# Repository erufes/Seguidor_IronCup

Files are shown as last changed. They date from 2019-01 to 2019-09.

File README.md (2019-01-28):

# Seguidor_IronCup
O objetivo deste projeto é construir e aprimorar um seguidor de linha capaz de ganhar a competição da IronCup 2019. Para isso, o projeto consta de estudo, prototipagem, desing e aprimoramento.  https://www.robocore.net/eventos/ironcup-2019  Edital da competição: https://www.robocore.net/upload/attachments/robocore__regras_seguidor_de_linha_108.pdf

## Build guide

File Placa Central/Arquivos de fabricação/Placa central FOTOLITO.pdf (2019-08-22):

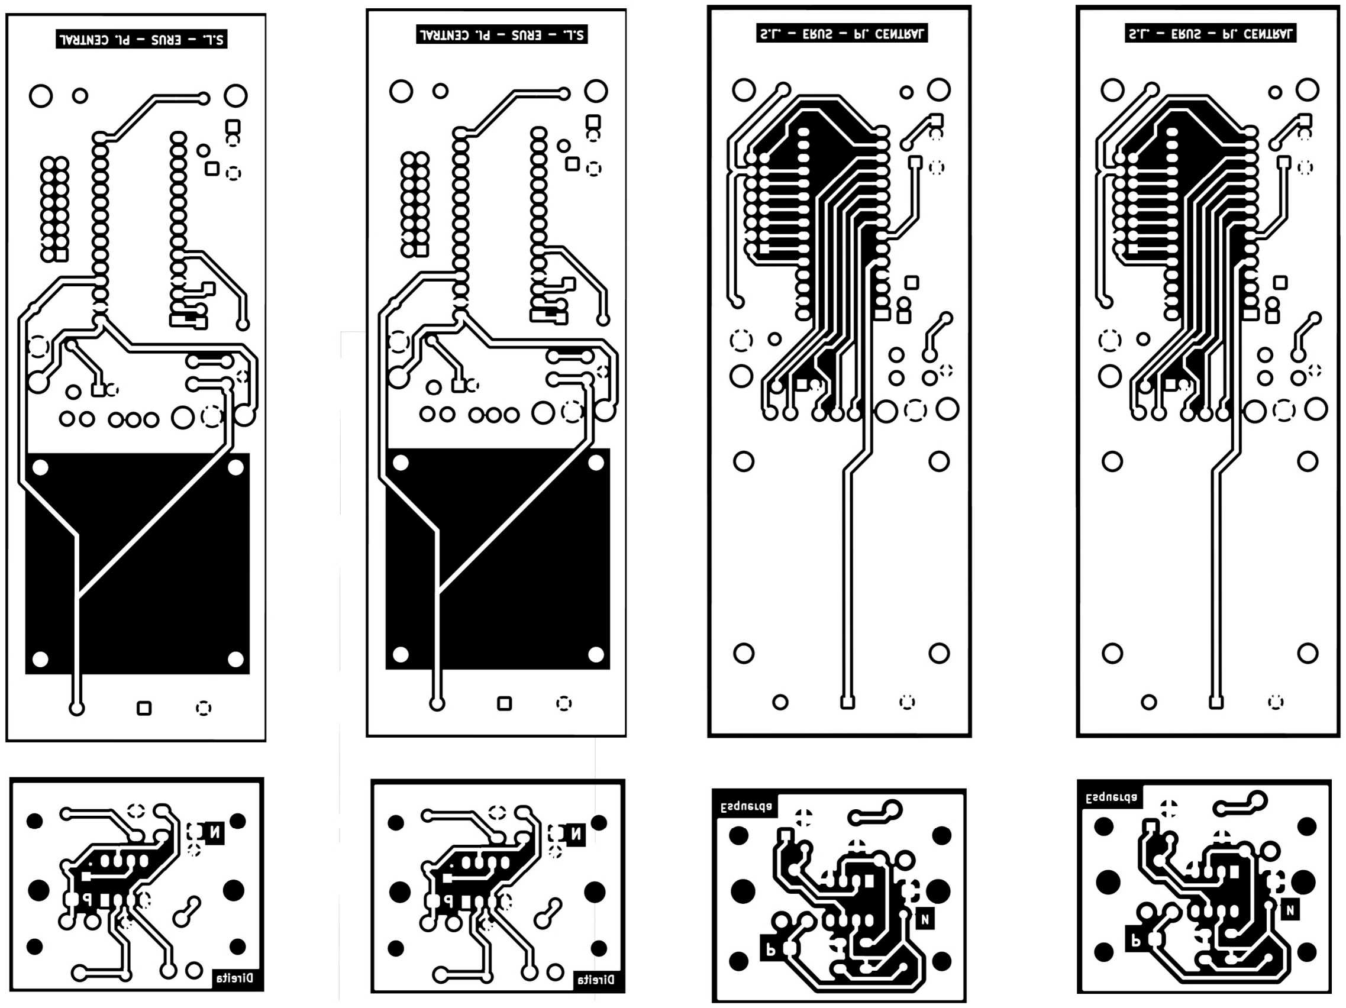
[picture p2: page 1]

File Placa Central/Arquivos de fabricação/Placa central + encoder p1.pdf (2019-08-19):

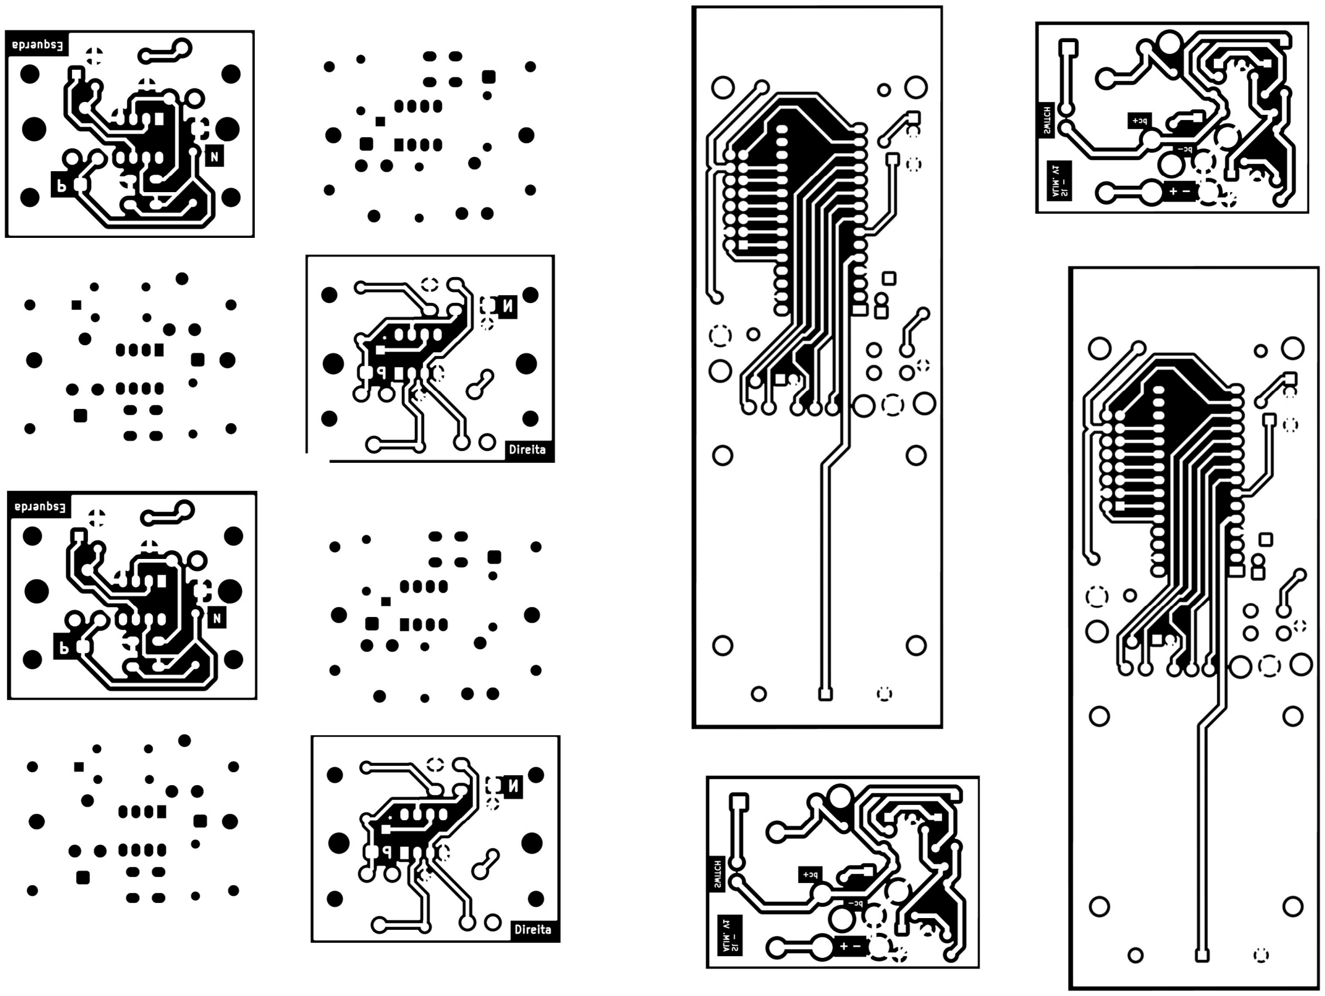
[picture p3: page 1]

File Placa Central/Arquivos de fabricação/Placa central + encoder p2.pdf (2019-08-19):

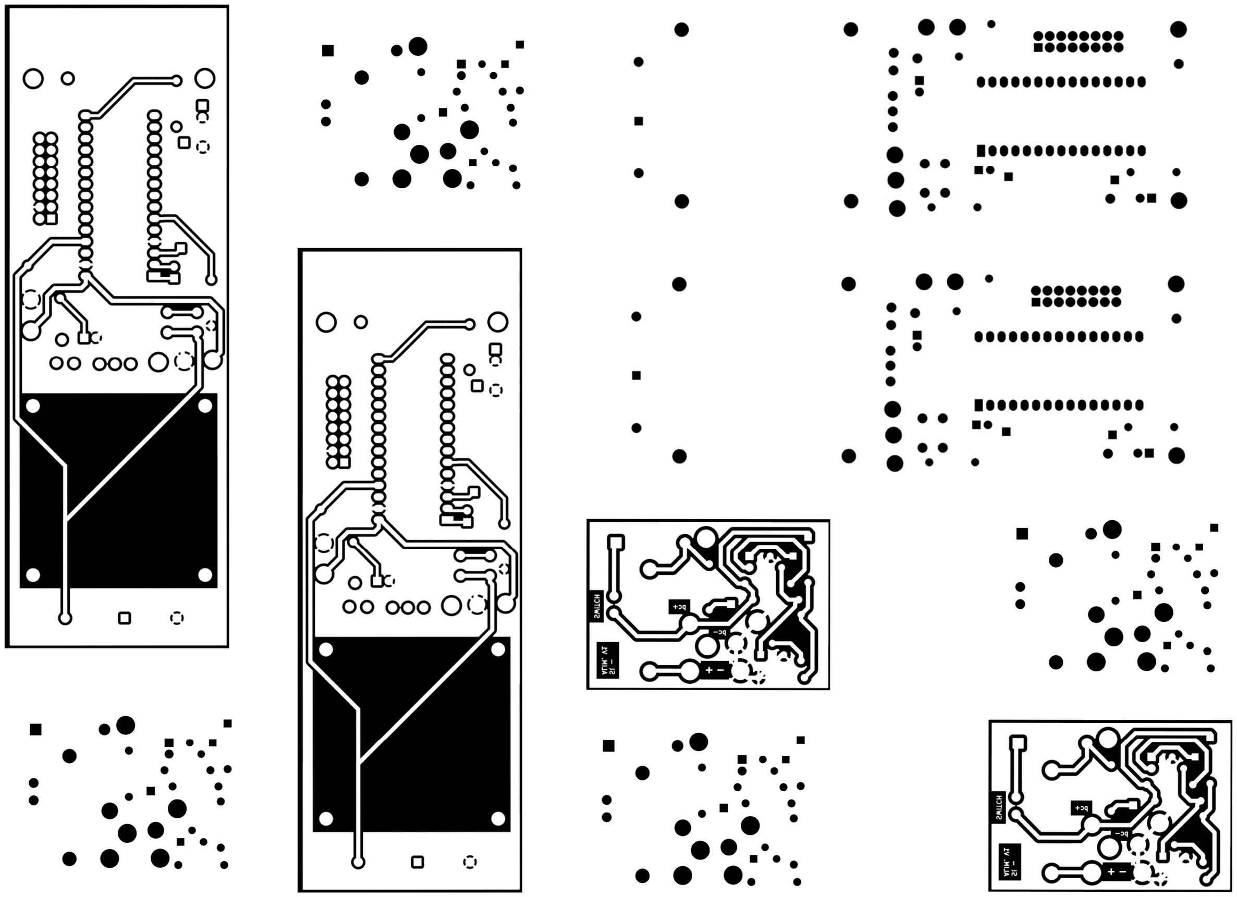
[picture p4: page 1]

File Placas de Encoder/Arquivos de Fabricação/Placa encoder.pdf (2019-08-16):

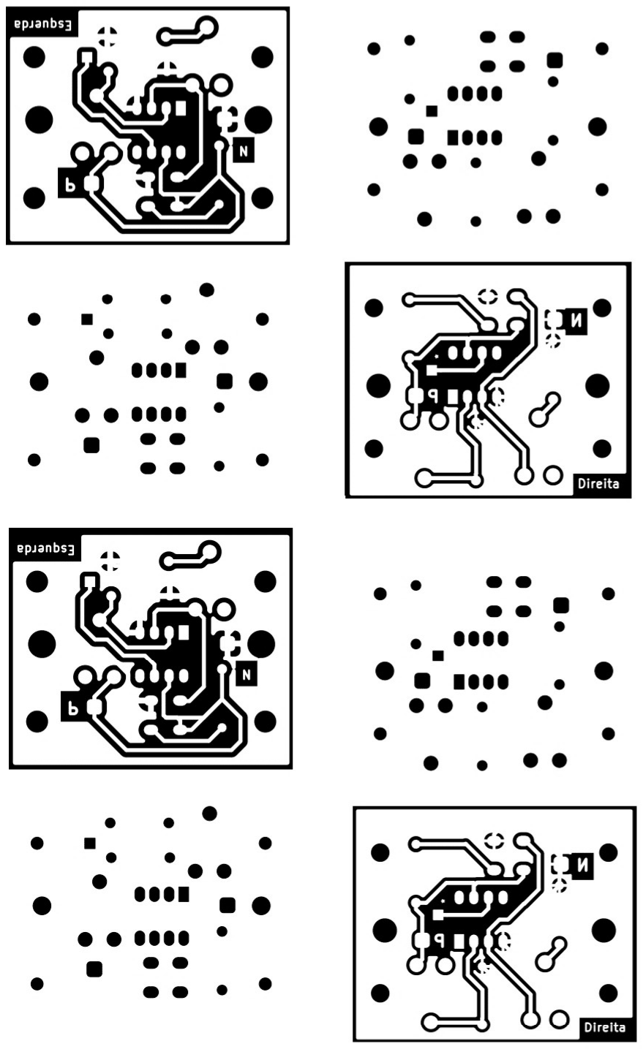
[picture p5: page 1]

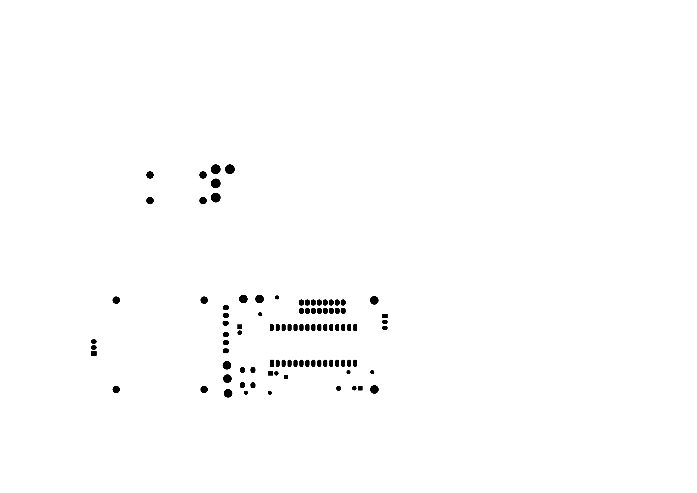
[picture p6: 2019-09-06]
Placa Central/Arquivos de fabricação/v1.1/Placa_central_v01-B_Mask_p001.png

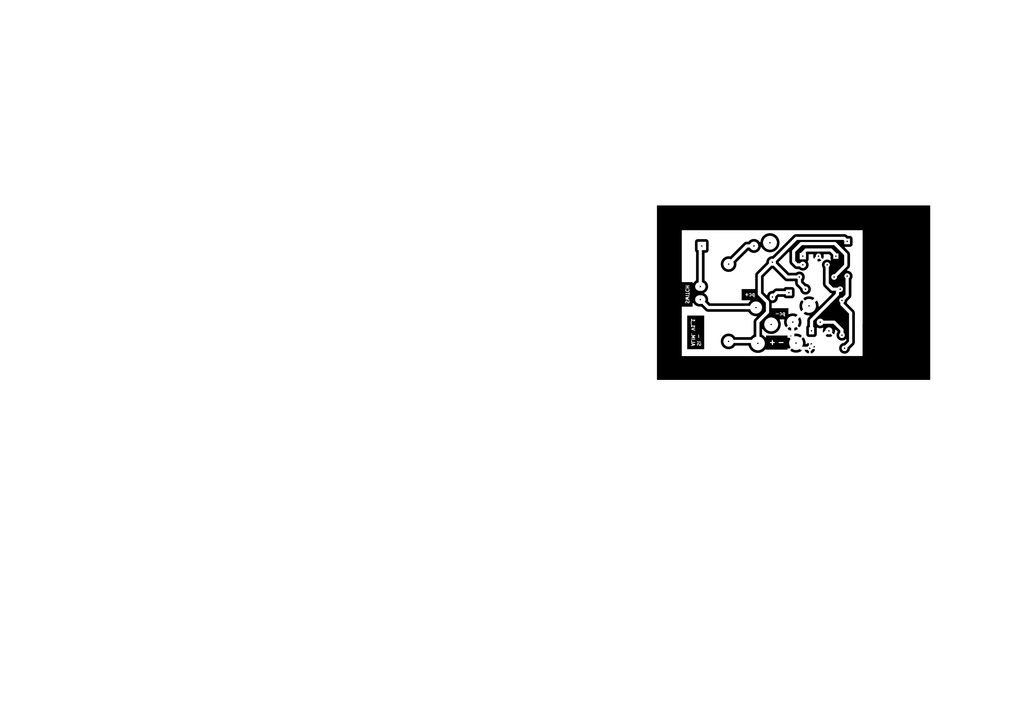
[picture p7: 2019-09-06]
Placa Central/Arquivos de fabricação/v1.1/Alimentacao e protecao-B_Cu_p001.png

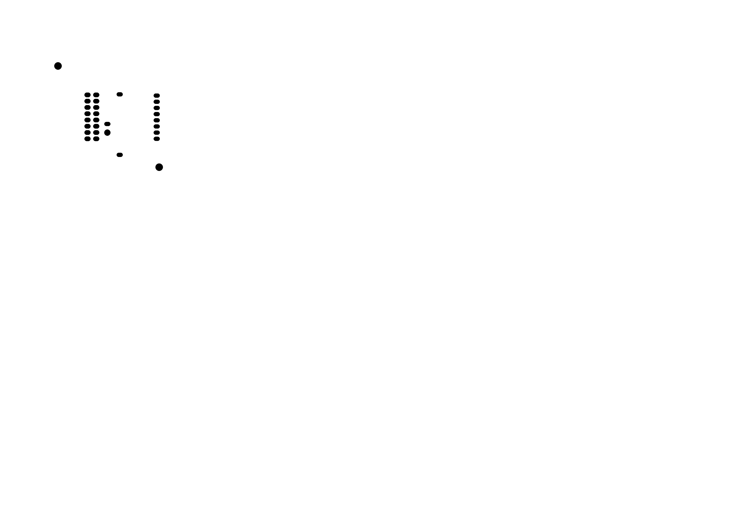
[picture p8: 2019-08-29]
Placa sensores/Placa_sensores v1_2/Placa de conexão/Arquivos de fabricação/Placa_sensores_v1_2 - Conector QTR-B_Mask_p001.png

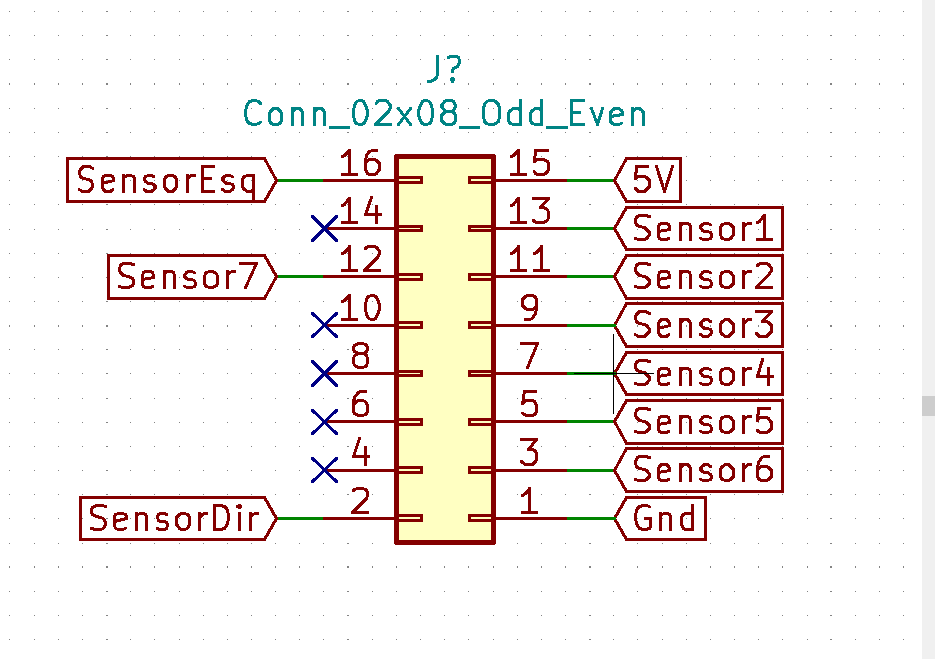
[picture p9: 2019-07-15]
Placa sensores/Placa_sensores v1_2/Placa de conexão/PrintConnectorPlacaSensores.png

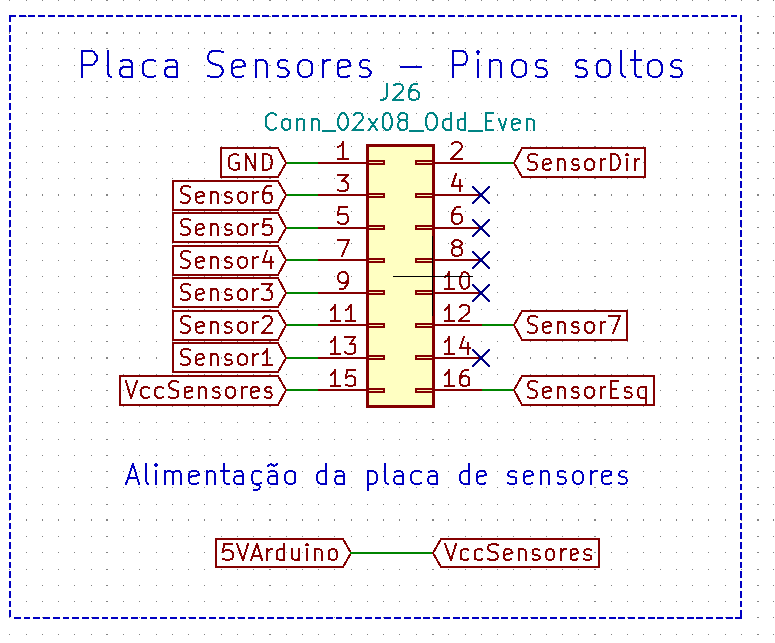
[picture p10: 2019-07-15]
Placa Central/PrintConnector.png

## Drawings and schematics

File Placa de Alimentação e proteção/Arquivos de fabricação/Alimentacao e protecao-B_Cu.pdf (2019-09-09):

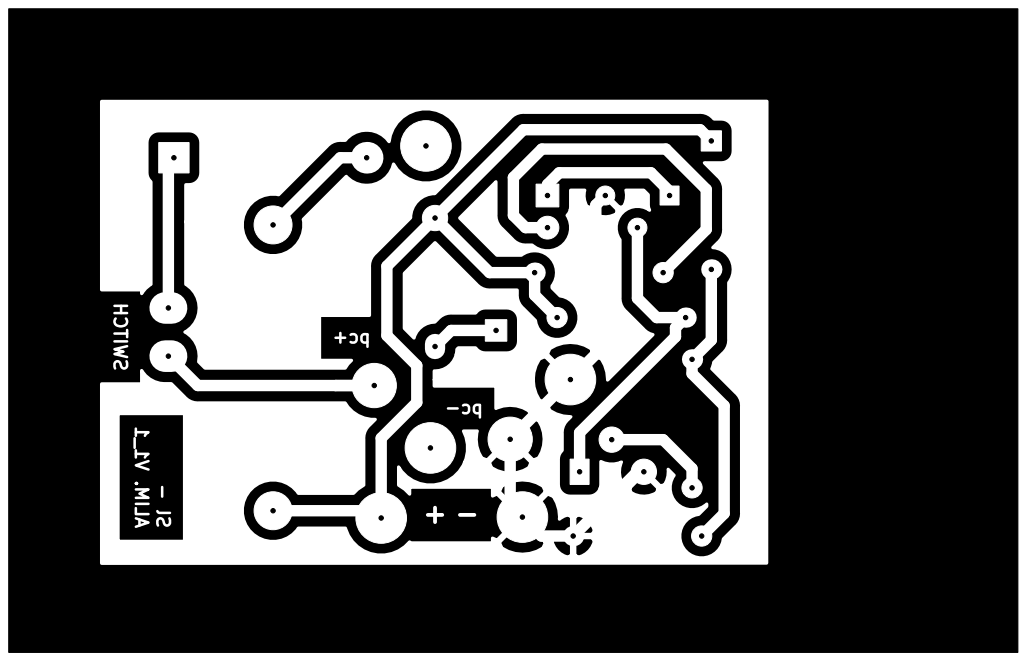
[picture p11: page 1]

ALIM. V1_1 Sl - + - pc+ pc- SWITCH

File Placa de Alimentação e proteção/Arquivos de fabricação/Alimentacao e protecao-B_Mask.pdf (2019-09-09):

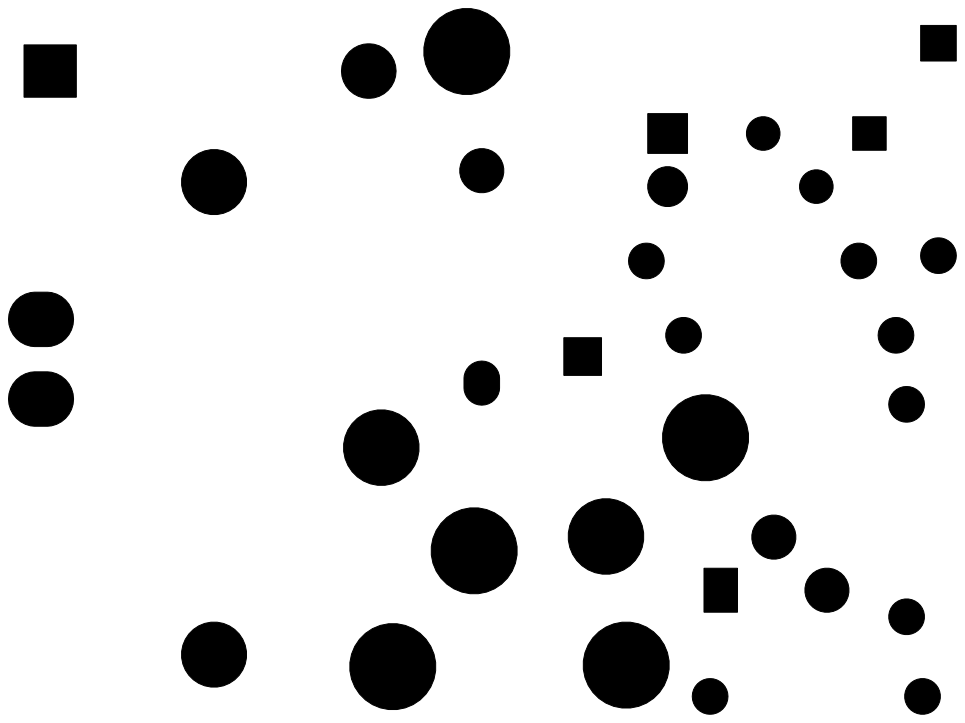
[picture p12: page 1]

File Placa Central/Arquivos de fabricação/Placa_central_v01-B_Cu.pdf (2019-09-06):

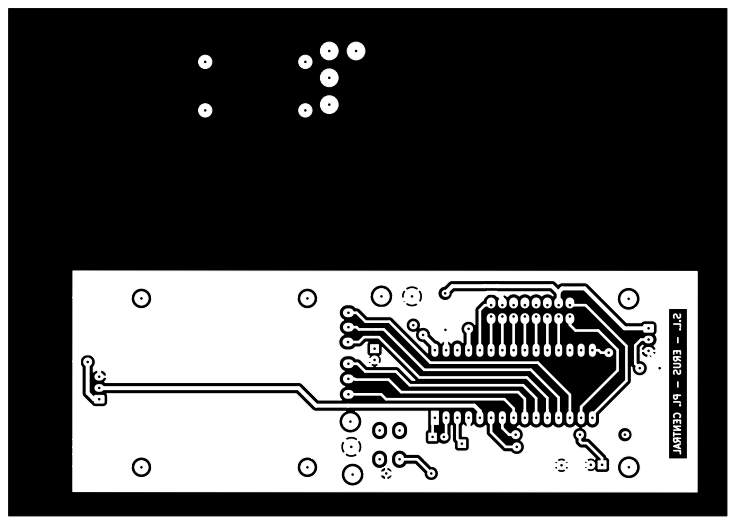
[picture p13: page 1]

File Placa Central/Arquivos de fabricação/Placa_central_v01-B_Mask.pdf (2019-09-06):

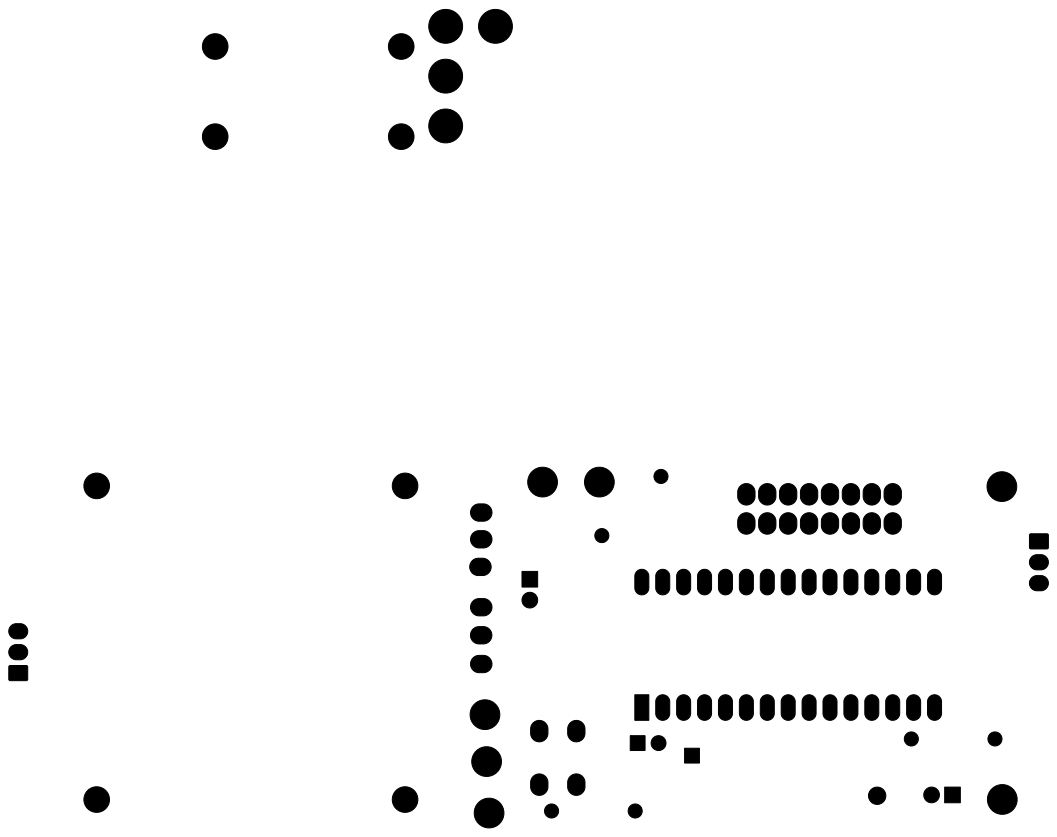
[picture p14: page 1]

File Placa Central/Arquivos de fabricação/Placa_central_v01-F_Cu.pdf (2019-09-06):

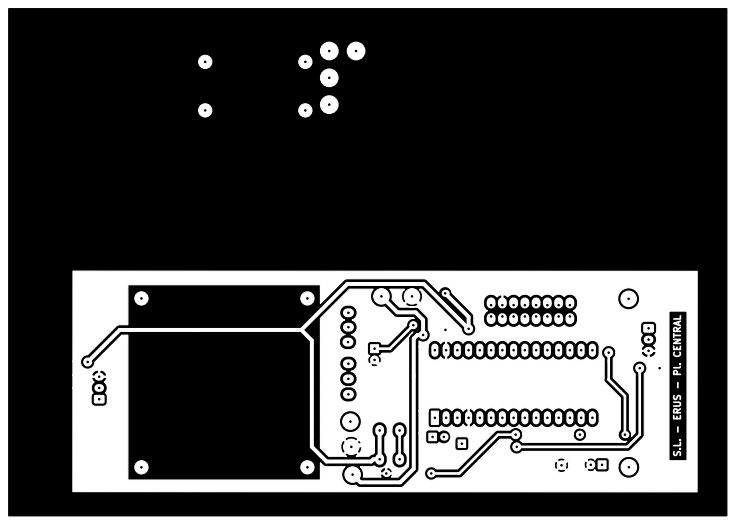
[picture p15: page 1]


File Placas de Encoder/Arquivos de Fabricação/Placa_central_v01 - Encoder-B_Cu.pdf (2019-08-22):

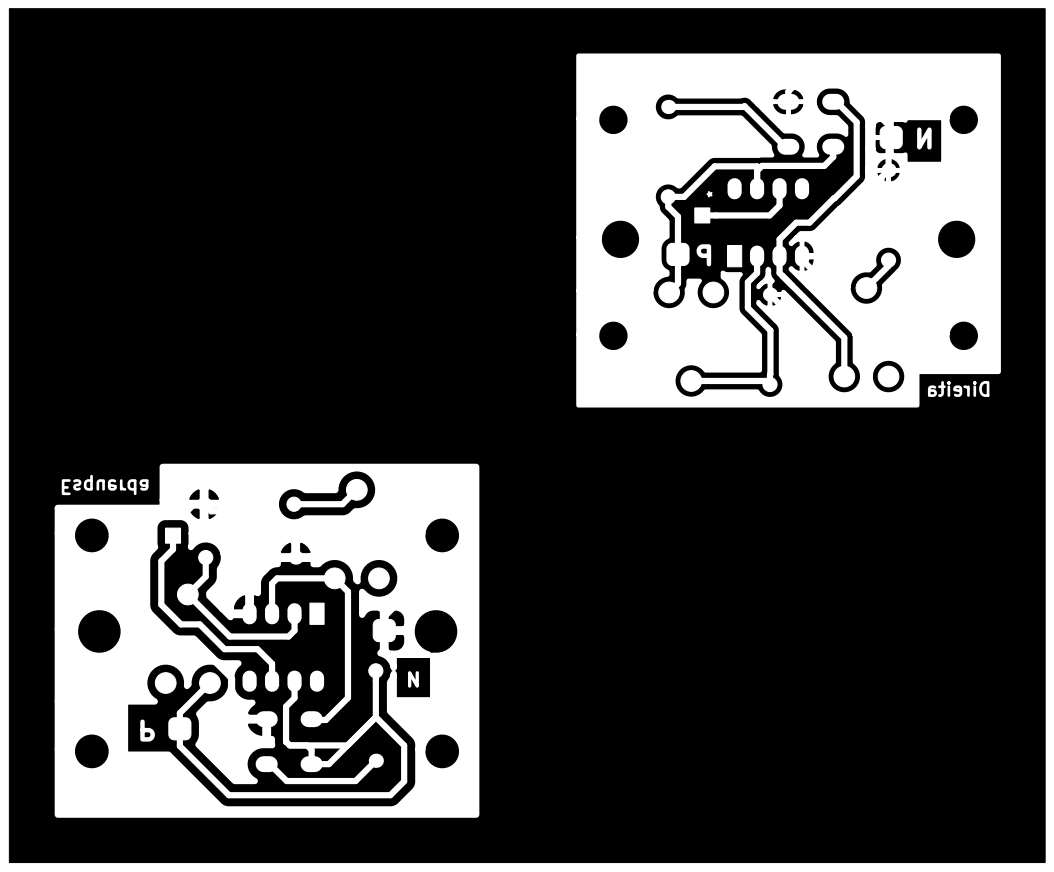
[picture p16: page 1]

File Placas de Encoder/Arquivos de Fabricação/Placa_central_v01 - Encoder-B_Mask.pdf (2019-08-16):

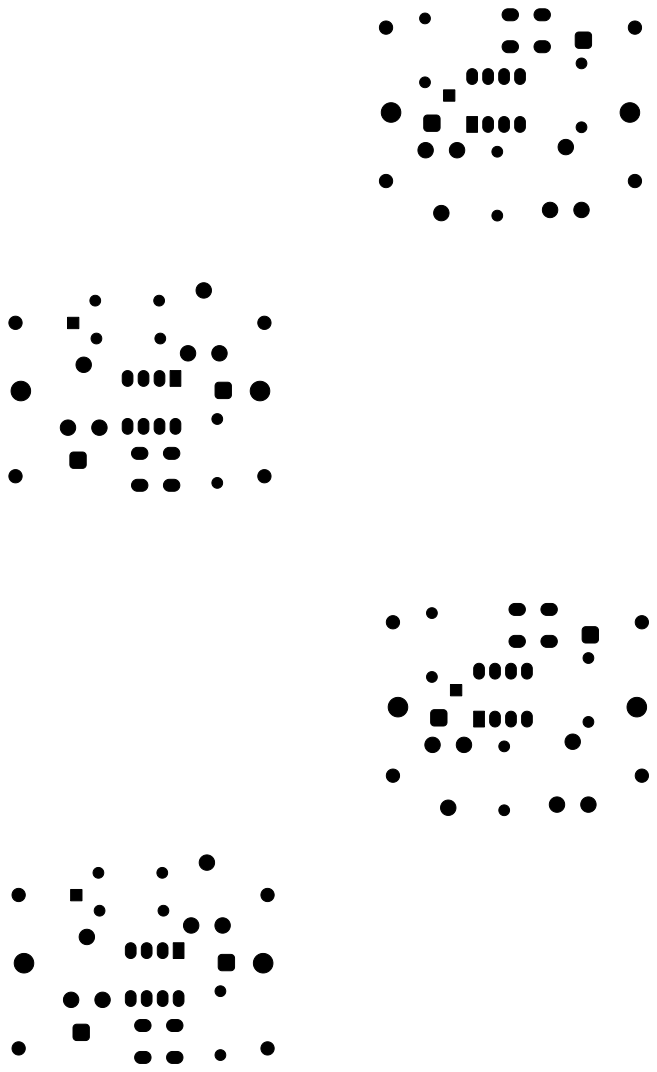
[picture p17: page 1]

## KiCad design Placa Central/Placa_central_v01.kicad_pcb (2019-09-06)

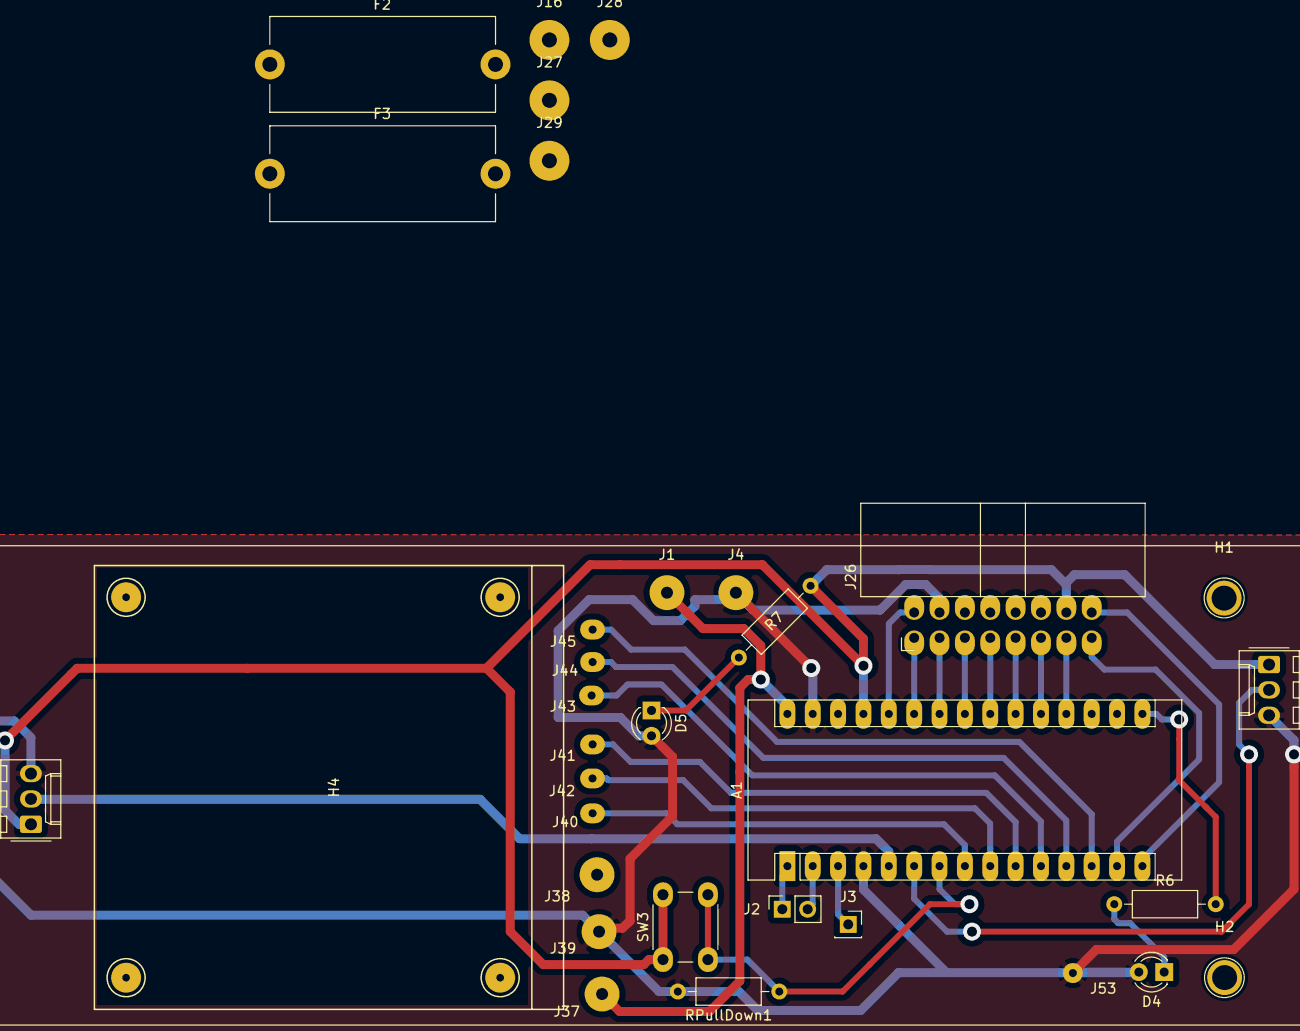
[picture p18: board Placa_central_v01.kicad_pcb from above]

Board: 2 copper layers, 33 parts (0 on the bottom side), 32 nets.

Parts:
A1: Arduino_Nano_v3.x; Arduino_Nano
D4: LedAzul; LED_D3.0mm
D5: LedVerde; LED_D3.0mm
F2, F3: Fuse-3A; Fuseholder_Cylinder-5x20mm_Stelvio-Kontek_PTF78_Horizontal_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
H1, H2: FuroPlaca; SolderWirePad_1x01_Drill2.5mm
H4: FurosPonteH; Ponte_H_furos
J1: Conn_8.4V_PlacaAlimentação; SolderWirePad_1x01_Drill1.2mm
J2: Conn_01x02_ArduinoTxRx; PinSocket_1x02_P2.54mm_Vertical
J3: Conn_01x01_ArduinoReset; PinSocket_1x01_P2.54mm_Vertical
J4: Conn_GND_PlacaAlimentação; SolderWirePad_1x01_Drill1.2mm
J5, J6: Conn_01x03_Female; Molex_KK-254_AE-6410-03A_1x03_P2.54mm_Vertical
J16: Conn_01x01_Motor1PonteHPCB; SolderWirePad_1x01_Drill1.5mm
J26: Conn_02x08_Odd_Even; IDC-Header_2x08_P2.54mm_Horizontal
J27: Conn_01x01_Motor2PonteHPCB; SolderWirePad_1x01_Drill1.5mm
J28: Conn_01x01_Motor1PCBMotor; SolderWirePad_1x01_Drill1.5mm
J29: Conn_01x01_Motor2PCBMotor; SolderWirePad_1x01_Drill1.5mm
J37: Conn_01x01_8.4VPonteH; SolderWirePad_single_1-2mmDrill
J38: Conn_01x01_5VPonteH; SolderWirePad_1x01_Drill1.2mm
J39: Conn_01x01_GNDPonteH; SolderWirePad_1x01_Drill1.2mm
J40: Conn_01x01_Motor1PWM; SolderWirePad_1x01_Drill0.8mm
J41: Conn_01x01_Motor1Dir1; SolderWirePad_1x01_Drill0.8mm
J42: Conn_01x01_Motor1Dir2; SolderWirePad_1x01_Drill0.8mm
J43: Conn_01x01_Motor2Dir1; SolderWirePad_1x01_Drill0.8mm
J44: Conn_01x01_Motor2Dir2; SolderWirePad_1x01_Drill0.8mm
J45: Conn_01x01_Motor2PWM; SolderWirePad_1x01_Drill0.8mm
J53: Conn_01x01_GNDEncoderDir; SolderWirePad_1x01_Drill0.8mm
R6: R330LedAzul; R_Axial_DIN0207_L6.3mm_D2.5mm_P10.16mm_Horizontal
R7: R330LedVerde; R_Axial_DIN0207_L6.3mm_D2.5mm_P10.16mm_Horizontal
RPullDown1: R10KPullDown; R_Axial_DIN0207_L6.3mm_D2.5mm_P10.16mm_Horizontal
SW3: SW_comando1; SW_PUSH_6mm_H5mm

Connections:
5VArduino: A1.27, J5.1, J6.1, J26.14, R7.2, SW3.1
8.4V: A1.30, J1.1, J37.1
Botao1: A1.7, RPullDown1.1, SW3.2
Encoder1: A1.5, J5.2
Encoder2: A1.6, J6.2
GND: A1.4, A1.29, D4.2, D5.2, J4.1, J5.3, J6.3, J26.4, J39.1, J53.1, RPullDown1.2
LedAzul: A1.16, R6.2
Motor1Dir1: A1.10, J41.1
Motor1Dir2: A1.9, J42.1
Motor1PWM: A1.8, J40.1
Motor2Dir1: A1.11, J43.1
Motor2Dir2: A1.12, J44.1
Motor2PWM: A1.13, J45.1
unnamed: D4.1, R6.1
unnamed: D5.1, R7.1
PCBMotor1_fused: F2.2, J28.1
PCBMotor2_fused: F3.2, J29.1
PonteHPCBMotor1: F2.1, J16.1
PonteHPCBMotor2: F3.1, J27.1
ResetArduino: A1.3, J3.1
Rx: A1.1, J2.1
Sensor1: A1.19, J26.13
Sensor2: A1.20, J26.11
Sensor3: A1.21, J26.9
Sensor4: A1.22, J26.7
Sensor5: A1.23, J26.5
Sensor6: A1.24, J26.3
Sensor7: A1.25, J26.1
Sensor8: A1.26, J26.2
SensorDir: A1.15, J26.16
SensorEsq: A1.14, J26.15
Tx: A1.2, J2.2

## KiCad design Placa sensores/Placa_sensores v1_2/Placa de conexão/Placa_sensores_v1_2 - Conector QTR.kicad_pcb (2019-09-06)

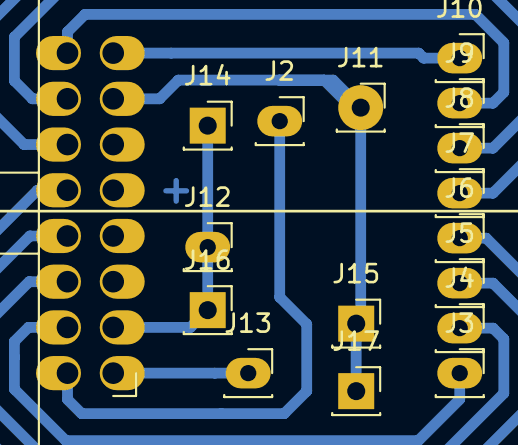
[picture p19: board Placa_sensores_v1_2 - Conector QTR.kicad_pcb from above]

Board: 2 copper layers, 21 parts (0 on the bottom side), 12 nets.

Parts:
H1, H1#2, H1#3, H2: MountingHole; MountingHole_3mm
J1: Conn_02x08_Odd_Even; IDC-Header_2x08_P2.54mm_Horizontal
J2, J3, J4, J5, J6, J7, J8, J9, J10, J11, J12, J13, J14, J15, J16, J17: Conn_01x01_Female; PinSocket_1x01_P2.54mm_Vertical

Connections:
GND: J1.13, J11.1, J15.1, J17.1
Sensor1: J1.4, J3.1
Sensor2: J1.6, J4.1
Sensor3: J1.8, J5.1
Sensor4: J1.10, J6.1
Sensor5: J1.12, J7.1
Sensor6: J1.14, J8.1
Sensor7: J1.16, J9.1
Sensor8: J1.15, J10.1
SensorDir: J1.1, J13.1
SensorEsq: J1.2, J2.1
VccSensores: J1.3, J12.1, J14.1, J16.1

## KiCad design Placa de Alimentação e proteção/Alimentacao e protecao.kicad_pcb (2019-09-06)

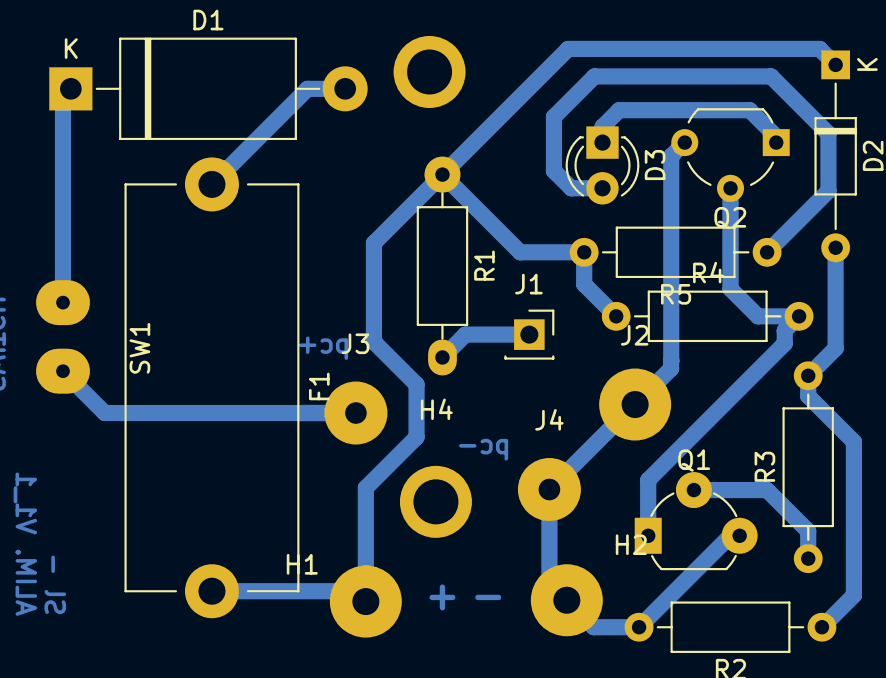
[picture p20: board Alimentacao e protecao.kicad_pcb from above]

Board: 2 copper layers, 20 parts (0 on the bottom side), 11 nets.

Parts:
D1: DiodoProtecao-5A; D_DO-27_P15.24mm_Horizontal
D2: DiodoZener6.8V; D_DO-35_SOD27_P10.16mm_Horizontal
D3: LedBateriaVermelho; LED_D3.0mm
F1: Fuse-5A; Fuseholder_Cylinder-5x20mm_Stelvio-Kontek_PTF78_Horizontal_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
H1: V8.4 - Lipo; SolderWirePad_1x01_Drill1.5mm
H2: GND - Lipo; SolderWirePad_1x01_Drill1.5mm
H3, H4: Furos; SolderWirePad_single_2-5mmDrill
J1: PinoCheckBateriaVcc; PinSocket_1x01_P2.54mm_Vertical
J2: PinoCheckBateriaGND; SolderWirePad_1x01_Drill1.5mm
J3: 8.4V_PlacaCentral; SolderWirePad_1x01_Drill1.2mm
J4: GND_PlacaCentral; SolderWirePad_1x01_Drill1.2mm
Q1, Q2: BC548; TO-92_Wide
R1: R10KBatCheck; R_Axial_DIN0207_L6.3mm_D2.5mm_P10.16mm_Horizontal
R2: R6K6MedidorDeBateria; R_Axial_DIN0207_L6.3mm_D2.5mm_P10.16mm_Horizontal
R3, R5: R1KMedidorDeBateria; R_Axial_DIN0207_L6.3mm_D2.5mm_P10.16mm_Horizontal
R4: R10KMedidorDeBateria; R_Axial_DIN0207_L6.3mm_D2.5mm_P10.16mm_Horizontal
SW1: SW_ON/OFF; Solder_Pad_Custom

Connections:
8.4VCircuitoMedidor: D2.1, F1.2, H1.1, R1.1, R4.1, R5.2
GND: H2.1, J2.1, J4.1, Q1.3, Q2.3, R2.2
unnamed: D1.1, SW1.2
unnamed: D1.2, F1.1
unnamed: D2.2, R2.1, R3.2
unnamed: D3.1, Q2.1
unnamed: D3.2, R5.1
unnamed: J1.1, R1.2
unnamed: J3.1, SW1.1
unnamed: Q1.1, Q2.2, R4.2
unnamed: Q1.2, R3.1

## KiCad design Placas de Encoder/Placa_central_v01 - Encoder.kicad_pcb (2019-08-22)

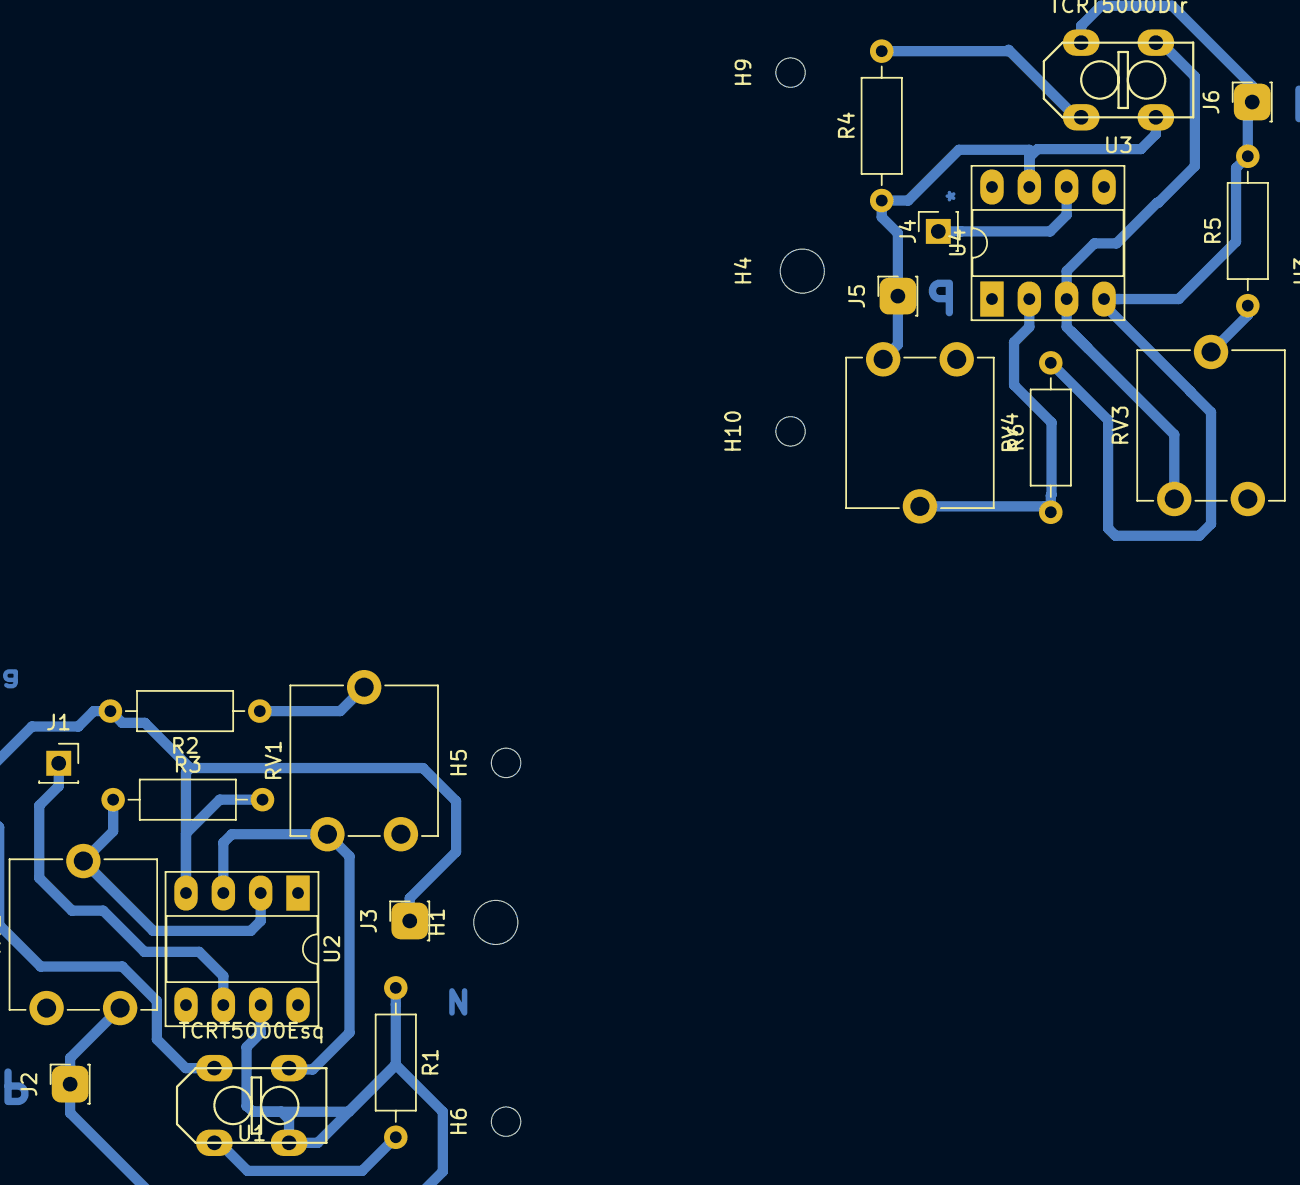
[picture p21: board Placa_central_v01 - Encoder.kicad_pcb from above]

Board: 2 copper layers, 32 parts (0 on the bottom side), 14 nets.

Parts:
H1: Furo1Esq; MountingHole_3mm
H2: Furo2Esq; MountingHole_3mm
H3: Furo1Dir; MountingHole_3mm
H4: Furo2Dir; MountingHole_3mm
H5: Furo3Esq; MountingHole_2mm
H6: Furo4Esq; MountingHole_2mm
H7: Furo5Esq; MountingHole_2mm
H8: Furo6Esq; MountingHole_2mm
H9: Furo3Dir; MountingHole_2mm
H10: Furo4Dir; MountingHole_2mm
H11: Furo5Dir; MountingHole_2mm
H12: Furo6Dir; MountingHole_2mm
J1, J2, J3, J4, J5, J6: Conn_01x01_Female; PinSocket_1x01_P2.54mm_Vertical
R1: R220ledIREsq; R_Axial_DIN0207_L6.3mm_D2.5mm_P10.16mm_Horizontal
R2: R1KEsq; R_Axial_DIN0207_L6.3mm_D2.5mm_P10.16mm_Horizontal
R3: R10kEsq; R_Axial_DIN0207_L6.3mm_D2.5mm_P10.16mm_Horizontal
R4: R220ledIRDir; R_Axial_DIN0207_L6.3mm_D2.5mm_P10.16mm_Horizontal
R5: R1KDir; R_Axial_DIN0207_L6.3mm_D2.5mm_P10.16mm_Horizontal
R6: R10k; R_Axial_DIN0207_L6.3mm_D2.5mm_P10.16mm_Horizontal
RV1, RV2: R10KPOT_TRIMEsq; Potentiometer_ACP_CA9-V10_Vertical
RV3: R10KPOT_TRIMDir; Potentiometer_ACP_CA9-V10_Vertical
RV4: R10KPOT_TRIM; Potentiometer_ACP_CA9-V10_Vertical
U1: TCRT5000Esq; TCRT5000Extendido
U2: LM741Esq; DIP-8_W7.62mm_Socket_LongPads
U3: TCRT5000Dir; TCRT5000Extendido
U4: LM741; DIP-8_W7.62mm_Socket_LongPads

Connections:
GNDDir: J6.1, R5.2, R6.2, U3.2, U4.4
GNDEsq: J3.1, R2.2, R3.2, U1.2, U2.4
unnamed: R1.2, U1.1
unnamed: R2.1, RV1.2
unnamed: R3.1, RV2.2, U2.2
unnamed: R4.2, U3.1
unnamed: R5.1, RV3.2
unnamed: R6.1, RV4.2, U4.2
unnamed: RV1.3, U1.4, U2.3
unnamed: RV3.3, U3.4, U4.3
SinalEncoderDIr: J4.1, U4.6
SinalEncoderEsq: J1.1, U2.6
VccDir: J5.e1, R4.1, RV4.1, U3.3, U4.7
VccEsq: J2.1, R1.1, RV2.1, U1.3, U2.7

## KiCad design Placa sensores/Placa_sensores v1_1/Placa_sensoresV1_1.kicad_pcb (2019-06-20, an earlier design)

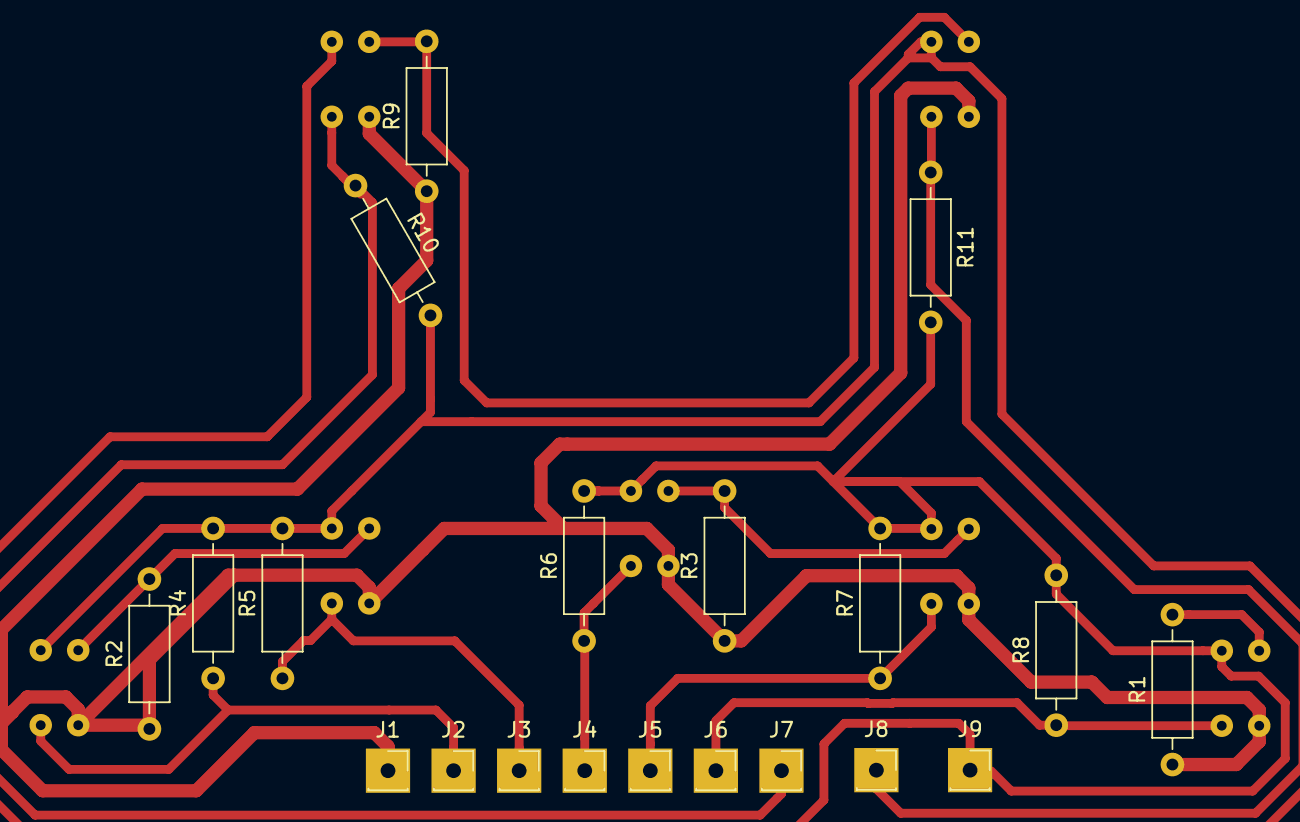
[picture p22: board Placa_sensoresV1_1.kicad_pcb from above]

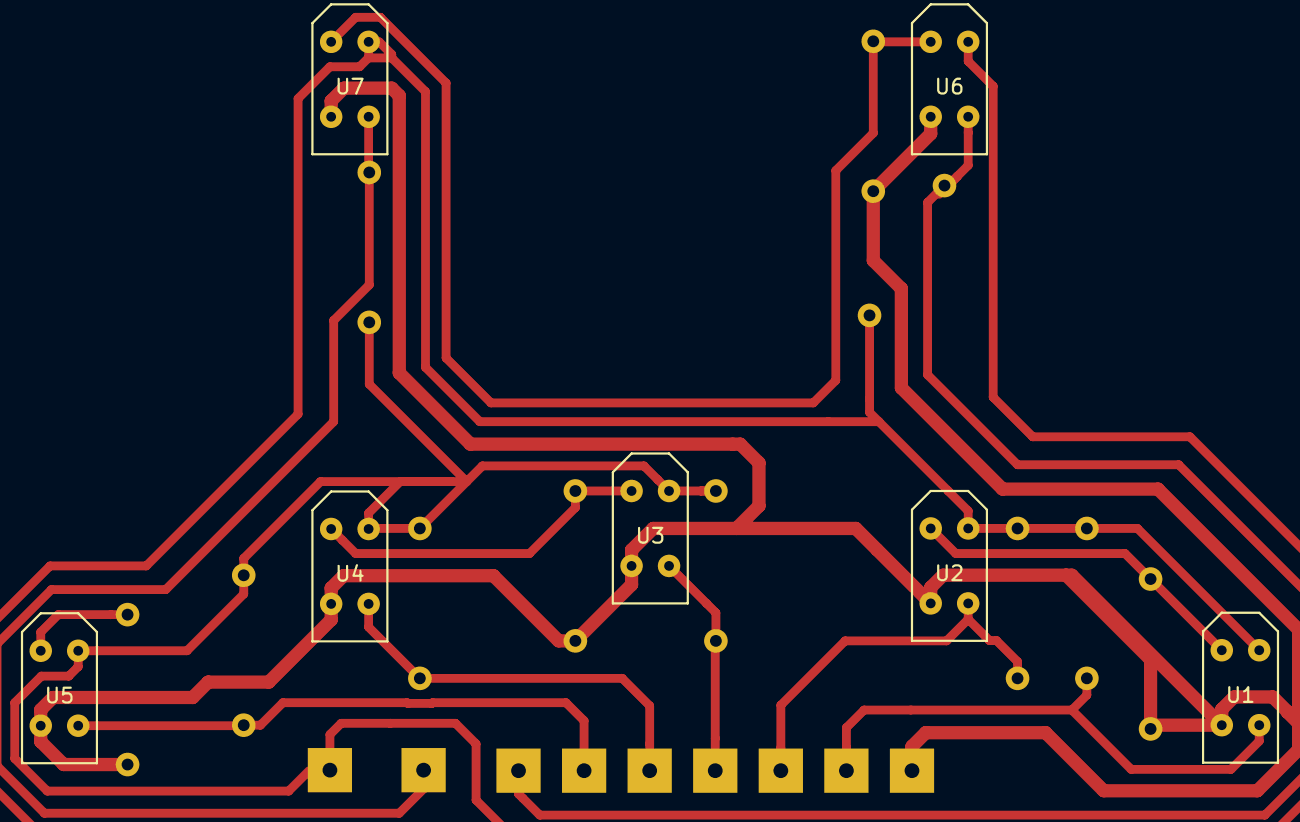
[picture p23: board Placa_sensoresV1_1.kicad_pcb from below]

Board: 2 copper layers, 27 parts (7 on the bottom side), 13 nets.

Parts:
J1, J2, J3, J4, J5, J6, J7, J8, J9: Conn_01x01_Female; PinSocket_1x01_P2.54mm_Vertical
R1, R2, R3, R9: 330; R_Axial_DIN0207_L6.3mm_D2.5mm_P10.16mm_Horizontal
R4, R5, R6, R7, R8, R10, R11: 10k; R_Axial_DIN0207_L6.3mm_D2.5mm_P10.16mm_Horizontal
U1, U2, U3, U4, U5, U6, U7: TCRT5000; TCRT50002

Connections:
GND: J9.1, R4.2, R5.2, R6.2, R7.2, R8.2, R10.2, R11.2, U1.2, U2.2, U3.2, U4.2, U5.2, U6.2, U7.2
unnamed: R1.2, U5.1
unnamed: R2.2, U1.1, U2.1
unnamed: R3.2, U3.1, U4.1
unnamed: R9.2, U6.1, U7.1
S1: J2.1, R4.1, U1.4
S2: J3.1, R5.1, U2.4
S3: J4.1, R6.1, U3.4
S4: J5.1, R7.1, U4.4
S5: J6.1, R8.1, U5.4
S6: J7.1, R10.1, U6.4
S7: J8.1, R11.1, U7.4
VCC: J1.1, R1.1, R2.1, R3.1, R9.1, U1.3, U2.3, U3.3, U4.3, U5.3, U6.3, U7.3

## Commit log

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2019-02-01 Corrigidos os nomes de variaveis no setup e loop.
    Código inicial terminado.
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2019-03-07 V1.01
    Adicionado as variáveis das bibliotecas.
    Começo do desenvolvimento do esquemático da pcb. Feito: módulo encoder; modulo 7805;
    [Placa_central_v01.kicad_pcb, Placa_central_v01.sch]
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2019-03-08 Placa com 7 sensores v1.1
    Commit de backup dos arquivos da placa antiga
    [Placa_sensore - Cópia.kicad_pcb, Placa_sensore Acertada for real.kicad_pcb, Placa_sensore Acertada v02.kicad_pcb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]
2019-03-08 V1.2.1 com Led on/off e Pad de gnd.
    Esquemático terminado e ja associado com os componentes.
    [Placa_sensores_v1_2.sch]
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2019-06-20 Aprimorado trabalho ja feito
    Separando os arquivos da maneira correta, criando a biblioteca, associando componentes certos, acertando questão de variáveis de PATH e etc.
    Tentativa de criar uma metodologia para as libraries e outros documentos do projeto.
    [Placa_central_v01.sch, Placa_sensore - Cópia.kicad_pcb, Placa_sensore Acertada for real.kicad_pcb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]
2019-06-20 Acertada mais questões de libraries
    Removi as que nao são necessárias e coloquei os componentes em novas bibliotecas, "Componentes soltos" para a pcb e "Sensores..." para o tcrt e o arduino.
    [Placa_central_v01.sch]
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2019-06-30 Terminado o esquemático do circuito
    Feito: circuito medidor de bateria; pads do arduino; pads do encoder; pads da ponte H; pads da placa de sensores;
    [Placa_central_v01.sch]
2019-06-30 Adicionado comp. fisíco BotãoOnOff
    Adicionado o relativo a pcb e seu 3d
    [_saved_Placa_central_v01.sch]
2019-06-30 Acertada nomeclatura do encoder
    De encoder1 para encoderEsq e a mesma coisa pro outro.
    [Placa_central_v01.sch, _saved_Placa_central_v01.sch]
2019-06-30 Pequenas mudanças
    Acertado nomeclatura de resistor; colocado um resistor no circuito de medição na tensão da bateria (separado do circuito de charga da bateria); gerado a lista de componentes (.csv)
    [Placa_central_v01.sch, Placa_central_v01_bom_.csv]
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2019-07-15 Acertado circuito e adicionado fusíveis
    Removido o circuito de carga da bateria; retirado os jack; adicionado os fusíveis; e antes de cada motor
    [Placa_central_v01.sch]
2019-07-15 Acertado a placa de sensores
    Acertado biblioteca, esquemático, conexão entre as placas e só.
    [Placa_central_v01.sch, Placa_sensores_v1_2.sch]
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2019-07-29 Adicionado Placa de Encoder
    Começado a placa.
    Tudo pronto para root, só falta isso
    [Placa_central_v01 - Encoder.kicad_pcb, Placa_central_v01 - Encoder.sch]
2019-07-30 Adicionado Furos a placa encoder. Falta root
    Adicionados os furos do suporte para o andar superior e para fixação no case do motor. Falta root
    [Placa_central_v01 - Encoder.kicad_pcb, Placa_central_v01 - Encoder.sch]
2019-07-31 Tentativa de root placa de encoder
    placa da direita rooteada e a placa da esquerda em processo.
    [Placa_central_v01 - Encoder.kicad_pcb, Placa_central_v01 - Encoder.sch]
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2019-07-31 Pinos J25(Led Azul) e J15 (ArduinoD6) retirados
    Esses pinos serão úteis para futuras expansões, porém suas conexões serão realocadas para o conector principal, e os pinos, para a placa de sensores
    [Placa_central_v01.sch]
2019-08-03 Distribuição dos compenentes praticamente concluída, quase pronta para root.
    Placa Central: 5VArduino(pino 15) colocado no pino 16, enquanto o sensorEsq(pino 16) foi colocado no pino 15 para
    facilitar o root; Adicionado na placa central os pads de conexao das alimentacoes provenientes do circuito de
    alimentacao; Label '5V' substituída por '5VArduino' - decisão a ser revisada; Pads de solda trocados por pads maiores
    por questoes de corrente alta (pinos de alimentacao). *Placa de Alimentação: Nome de dois pinos da placa de alimentação
    modificados. Pads de solda trocados por pads maiores por questoes de corrente alta (pinos de alimentacao).
    [Alimentacao e protecao.kicad_pcb, Alimentacao e protecao.sch, Placa_central_v01.kicad_pcb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]
2019-08-05 Separação do projeto do encoder em pasta
    Separação em uma pasta separada e preparação da placa de encoder para impressão.
    [Placa_central_v01 - Encoder.kicad_pcb, Placa_central_v01 - Encoder.sch]
2019-08-06 Root finalizado, aguardando revisão dos demais membros. Ocorreram mudanças massivas nas conexões de pinos lógicos e do conector.
    Track Width (grossura da linha) modificado para 0,9 mm na placa central. Conexões do Conector rearranjadas.
    Tag 'Botão1' movida para o pino 6;
    Tag 'Arduino13' (agora vago - pino 16) adicionado ao conector;
    Pino ArduinoD13 será adicionado ao conector (se possível), para possível uso futuro. Outros pinos extras não serão adicionados. O pino será de fato adicionado na PBC dos sensores.
    Tag 'Motor1Pwm' movida para o pino 13;
    Tag 'Motor2Dir2' movida para o pino 12;
    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
    [Placa_central_v01.kicad_pcb, Placa_central_v01.sch]
2019-08-07 Feito cópia do projeto da PBC Central com novo root contendo mudanças nas Clearances e Track Widths.
    Criada nova pasta com cópia da placa central - nova tentativa de root com dimensões diferentes;
    Track Width padrão modificada para 0.6 mm;
    Clearance padrão modificada para 0.6 mm;
    Criado novo conjunto de net class 'POWER' - utilizado para trilhas de alimnentação;
    Criado novo conjunto de net class 'Critical Long trails' - utilizado para trilhas muito longas e críticas para o funcionamento do circuito.
    [Placa_central_v01.kicad_pcb, Placa_central_v01.sch, Placa_central_v01_bom_.csv]
2019-08-07 Removido tentativa anterior de root, projeto da placa central foi unificado
    Nova tentativa de root bem sucedida, root anterior foi excluído.
    Os fusíveis dos motores foram removidos da placa central e serão adicionados nas placas de encoder de cada motor.
    [Placa_central_v01.kicad_pcb, Placa_central_v01.sch, Placa_central_v01_bom_.csv]
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2019-08-07 Adicionada a zona de malha de ground, furos pendentes.
    A zona de ground ainda não foi preenchida pois os furos da placa para fixação no acrílico requerem atualização.
    [Placa_central_v01.kicad_pcb, Placa_central_v01.sch]
2019-08-14 Tamanho dos pinos corrigidos
    [Placa_central_v01.kicad_pcb, Placa_central_v01.sch]
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2019-09-04 Mudancas criticas na PCB Central, ainda ha pendencias
    Foi trocado o pino do botao pelo pino do encoder. Os encoders devem estar obrigatoriamente nos pinos D2 e D3:
    Encoder2 para o pino 6 (D3)
    Botao1 para o pino 7 (D4);
    Aumentadas as dimensoes dos pads conectores do arduino, para mais seguranca ao furar;
    Pads do conector modificados para melhor seguranca ao furar;
    Clearance da malha de ground aumentada de 0.5 para 0.7
    [Placa_central_v01.kicad_pcb, Placa_central_v01.sch]
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2019-09-16 Iniciado projeto de placa unificada do seguidor de linha
    Foram criados esquematicos hierarquizados de cada um dos modulos. Os esquematicos foram importados num projeto unico chamado "Seguidor_V1".
    A ideia de unificar as placas visa simultaneamente reduzir peso e dimensoes do chassi, ao mesmo tempo em que elimina problemas comuns de conexao e solda entre placas, simplificando como um todo a execucao do projeto e aumentando a eficiencia do robo.
    Ainda serao necessarias varias alteracoes no projeto, em especial:
    Utilizar um processador ATMega embarcado diretamente;
    Utilizar um ATMega com mais pinos disponiveis;
    Sera necessario substituir as conexoes entre placas, de fios para trilhas
    Todas a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
    [Alimentacao e protecao.sch, Placa_central_v01 - Encoder.sch, Placa_central_v01.sch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]
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2022-09-01 Exclusão da DRV8833 e várias pequenas mudanças
    Exclusão da DRV8833 e do jumper de seleção de ponte H.
    Alteração do esquemático da bateria;
    Alteração no tamanho dos furos de alinhamento, para usar com os pinos de aço de 2,5mm e 3mm.
    Adicionado pad intermediário entre baterias para medição via pad.
    Corrigido circuito de enable.
    Corrigido circuito de led Tx e Rx.
